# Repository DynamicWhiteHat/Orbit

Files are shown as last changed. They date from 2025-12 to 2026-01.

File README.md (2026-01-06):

# Orbit
## An ESP32-powered mini drone with autonomous following capability

## Features:
- ESP32 S3 Wroom 1u SoM
- 4x 0716 coreless motors
- MPU6050 for gyro
- QMC5883 compass
- MS5611 pressure sensor for altitude hold
- 3x SK6812 for signal LEDs
- Battery charging via USB-C
- 2x frame mounted DWM1000 for position tracking
- 1x small form factor DWM1000 board "beacon"
- Firmware based on flix by okalachev, modified to work with this project

## Why I designed this project:
I wanted to design a drone for HackClub's Blueprint program, but not just any regular drone. I wanted to add a feature that would make it stand out, something that would make it unique. So, I decided to give it the ability to autonomously follow you to an accurate degree. After doing some research, I found the DWM1000 modules and decided to design this project. I designed and redesigned the PCBs and CAD for this project many times, with each iteration improving upon the last. This project also gave me the ability to test and improve my PCB and CAD design skills. I understood a lot more about schematic connections while working on this project and learned to route much cleaner traces, even on a compact board.

## Image gallery:
<table align="center">
  <tr>
    <td align="center">
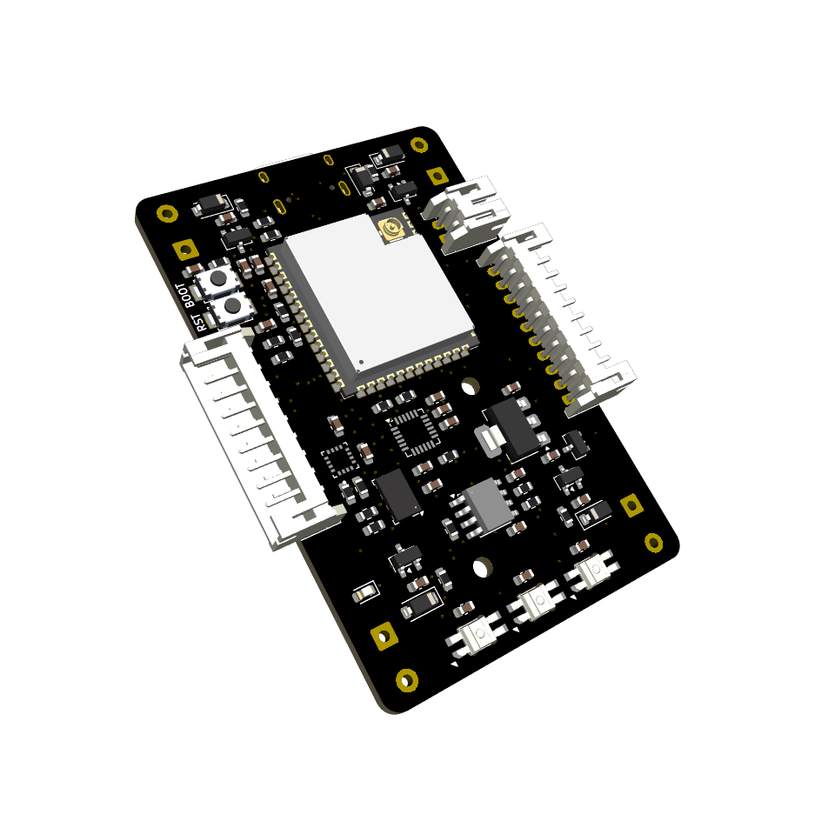
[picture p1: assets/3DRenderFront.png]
      
    </td>
    <td align="center">
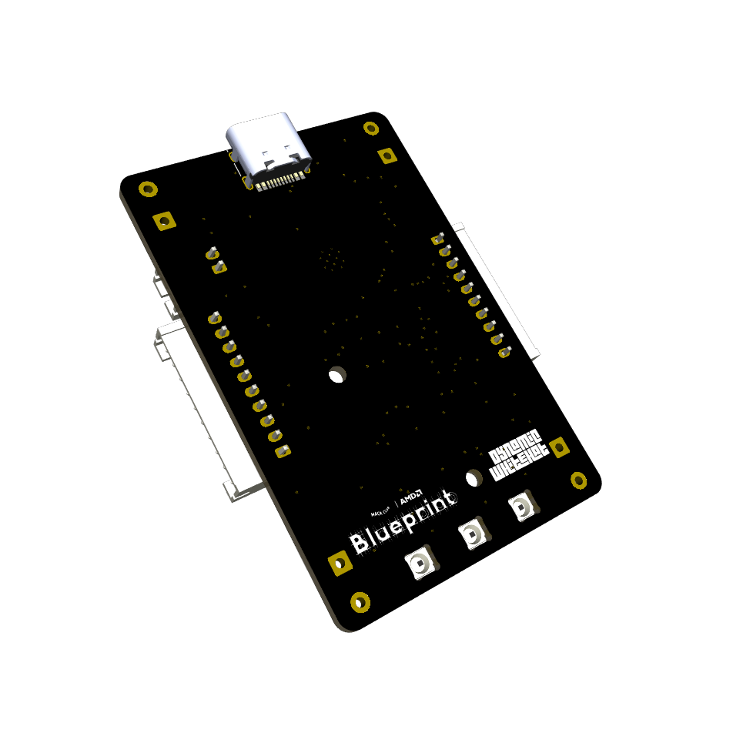
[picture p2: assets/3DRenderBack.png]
      
    </td>
  </tr>
  <tr>
    <td align="center" colspan="2">
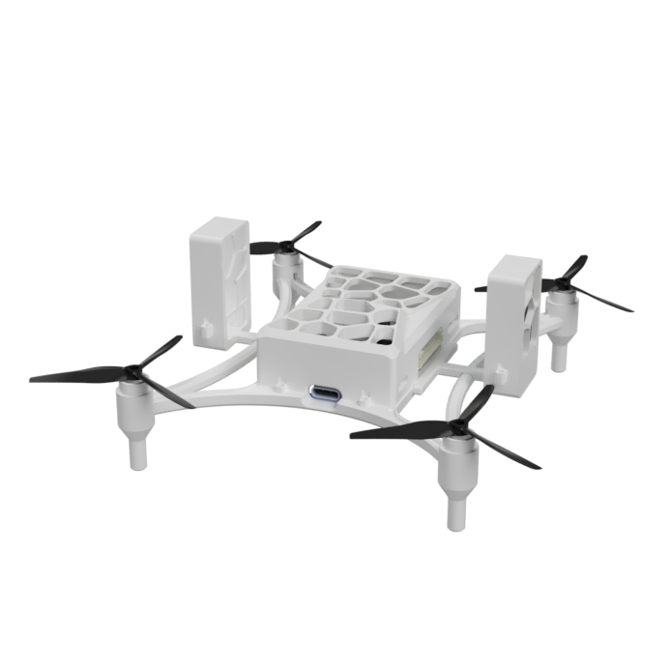
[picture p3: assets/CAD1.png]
      
    </td>
  </tr>
</table>

## Schematics And PCBS

<details>
<summary>Drone Control Board</summary>
<table align="center">
  <tr>
    <td align="center" colspan="2">
      
    </td>
  </tr>
  <tr>
     <td align="center">
      
    </td>
    <td align="center">
      
    </td>
  </tr>
</table>
</details>

<details>
<summary>Beacon Board</summary>
<table align="center">
  <tr>
    <td align="center" colspan="2">
      
    </td>
  </tr>
  <tr>
     <td align="center">
      
    </td>
    <td align="center">
     
    </td>
  </tr>
</table>
</details>

<details>
<summary>UWB Module Board</summary>
<table align="center">
  <tr>
    <td align="center" colspan="2">
      
  </tr>
  <tr>
     <td align="center">
      
    </td>
    <td align="center">
      
    </td>
  </tr>
</table>
</details>

## How It Works

The drone is powered by a custom designed PCB based on the ESP-32 S3 Wroom 1u SoM. It includes three SK6812 mini-e LEDs to serve as a status signal, located at the rear of the drone. There are three sensors located on board to help with flight. The MPU-6050 is a triple-axis accelerometer and gyroscope that is essential to help the drone fly. The MS5611 is a pressure sensor that is used to record and maintain height during flight. The final sensor, an HMC5883, is a triple-axis magnetometer that is used to report the drone's heading. The latter two sensors are reported in QGroundControl or any other flight operating station to provide information to the controller. The 0716 coreless motors are powered by a simple MOSFET circuit, designed by MaxImagination. This circuit has a small footprint and fits great for small projects, such as this drone. Autonomous flight is achieved using two DWM1000 modules mounted on the sides of the drone. These were implemented on the main PCB using 10-pin JSTs to allow modular connectivity, allowing the controller to select whether to fly with or without the ranging sensors. The DWM1000s mounted on the drone communicate with an external DWM1000 "beacon" that is with the controller or person of interest. This beacon is encased in a watch case to make it easy to wear. By sending messages between the modules, the distance between them can be calculated, allowing the beacon's location to be triangulated. This location is then set in the PID controllers, allowing the drone to autonomously navigate.

## Bill Of Materials

| Item | Description | Quantity | URL | Unit Price ($) | Total Price ($) |
|---|---|---|---|---|---|
| DWM1000 | Ranging Modules | 3 | https://www.aliexpress.us/item/3256808347510093.html | $15.13 | $50.90 |
| XIAO ESP-32 | For Beacon | 1 | Already Have | | |
| LCSC | PCB Components | 1 Order of All Parts | See LCSC BOM | | $36.92 |
| JST Connector | For DWM Connection | 1 Pack of 10 | https://www.aliexpress.us/item/3256805775471278.html | $3.09 | $3.09 |
| Battery | For Beacon | 1 | https://www.amazon.com/AKZYTUE-Battery-Rechargeable-Lithium-Connector/dp/B07TXJ4C46 | $7.79 | $7.79 |
| Battery | For Drone | 1 | https://www.amazon.com/EEMB-Battery-Rechargeable-Lithium-Connector/dp/B0B7R8CS2C | $6.99 | $7.99 |
| Motors | For Drone | 1 Pack of 4 | https://www.amazon.com/Coliao-Coreless-19000KV-Propeller-Quadcopter/dp/B0CHYDJMF2/  | $10 | $11 |
| Antenna | For Drone | 1 | https://www.aliexpress.us/item/3256806233080373.html | $1.64 | $1.64 |
| Screws | To Hold Case | 1 Pack | https://www.aliexpress.us/item/3256806233080373.html | $5.90 | $5.90 |
| JLCPCB Order  | PCBs | 1 | JLCPCB Quote | $17.16 | $17.16 |
| | | | | | $139.08 |

### LCSC Bill Of Materials
| Description | Quantity Needed | Mrf# | Minimum Order Qty. | Unit Price(USD) | Ext.Price(USD) | LCSC# | Product Link |
|---|---|---|---|---|---|---|---|
| N-Channel 20V 4A 1.2W Surface Mount SOT-23 | 4 | SI2300 | 20 | 0.0164 | 0.33 | C5224175  | https://www.lcsc.com/product-detail/C5224175.html  |
| QFN-24-EP(4x4) Accelerometers RoHS | 1 | MPU-6050 | 1 | 6.8489 | 6.85 | C24112 | https://www.lcsc.com/product-detail/C24112.html |
| 1Kpa~1.2bar QFN-8(3x5) Pressure Sensors, Transducers RoHS | 1 | MS561101BA03-50 | 1 | 5.5485 | 5.55 | C15639 | https://www.lcsc.com/product-detail/C15639.html |
| I2C LGA-16(3x3) Linear, Compass (ICs) RoHS | 1 | QMC5883P | 1 | 1.4485 | 1.45 | C2847467  | https://www.lcsc.com/product-detail/C2847467.html  |
| Red LED Indication - Discrete 2.7V~3.2V 0602 | 5 | YLED0603R | 200 | 0.0055 | 0.55 | C19171390 | https://www.lcsc.com/product-detail/C19171390.html |
| Emerald Green LED Indication - Discrete 2.7V~3.2V 0603 | 13 | YLED0603G | 200 | 0.0054 | 1.08 | C19273151 | https://www.lcsc.com/product-detail/C19273151.html |
| 2.4GHz ESP32-S3R8 -98.2dBm SMD,19.2x18mm RF Transceiver Modules and Modems RoHS | 1 | ESP32-S3-WROOM-1U-N16R8 | 1 | 5.3260 | 5.33 | C3013946  | https://www.lcsc.com/product-detail/C3013946.html  |
| 100nF ±10% 50V Ceramic Capacitor X7R 0603 | 17 | CC0603KRX7R9BB104 | 100 | 0.0025 | 0.25 | C14663 | https://www.lcsc.com/product-detail/C14663.html |
| 220nF ±10% 50V Ceramic Capacitor X7R 0603 | 1 | CL10B224KB8NNNC | 100 | 0.0081 | 0.81 | C64705 | https://www.lcsc.com/product-detail/C64705.html |
| 4.7uF ±10% 10V Ceramic Capacitor X5R 0603 | 3 | CL10A475KP8NNNC | 50 | 0.0051 | 0.26 | C1705 | https://www.lcsc.com/product-detail/C1705.html |
| 10uF ±10% 10V Ceramic Capacitor X5R 0603 | 17 | CL10A106KP8NNNC | 50 | 0.0058 | 0.29 | C19702 | https://www.lcsc.com/product-detail/C19702.html |
| 1uF ±10% 50V Ceramic Capacitor X5R 0603 | 1 | CL10A105KB8NNNC | 50 | 0.0049 | 0.25 | C15849 | https://www.lcsc.com/product-detail/C15849.html |
| 10nF ±10% 50V Ceramic Capacitor X7R 0603 | 2 | CC0603KRX7R9BB103 | 100 | 0.0022 | 0.22 | C100042 | https://www.lcsc.com/product-detail/C100042.html |
| Diode Independent 100V 300mA Surface Mount SOD-123 | 4 | 1N4148W | 100 | 0.0056 | 0.56 | C917030 | https://www.lcsc.com/product-detail/C917030.html |
| Diode Array 1 Pair Common Cathode 30V 200mA Surface Mount SOT-23 | 1 | BAT54C | 50 | 0.0063 | 0.32 | C916424 | https://www.lcsc.com/product-detail/C916424.html |
| Diode 40V 1A Surface Mount SOD-123 | 1 | 1N5819HW | 20 | 0.0237 | 0.47 | C5439970  | https://www.lcsc.com/product-detail/C5439970.html  |
| USB-C (USB TYPE-C) Receptacle Connector 16 Position Surface Mount | 1 | TYPE-C-31-M-12 | 5 | 0.1762 | 0.88 | C165948 | https://www.lcsc.com/product-detail/C165948.html |
| 100mW 10kΩ 75V ±100ppm/℃ Thick Film Resistor ±1% 0603 Chip Resistor - Surface Mount RoHS | 14 | RC0603FR-0710KL | 100 | 0.0011 | 0.11 | C98220 | https://www.lcsc.com/product-detail/C98220.html |
| 5.1kΩ ±1% 100mW 0603 Thick Film Resistor | 2 | FRC0603F5101TS | 100 | 0.0009 | 0.09 | C2907044  | https://www.lcsc.com/product-detail/C2907044.html  |
| 400mΩ ±1% 100mW 0603 Thick Film Resistor | 1 | FRL0603FR400TS | 100 | 0.0033 | 0.33 | C5126047  | https://www.lcsc.com/product-detail/C5126047.html  |
| 1kΩ ±1% 100mW 0603 Thick Film Resistor | 10 | FRC0603F1001TS | 100 | 0.0009 | 0.09 | C2907002  | https://www.lcsc.com/product-detail/C2907002.html  |
| 5kΩ 100mW 75V ±50ppm/℃ Thin Film Resistor ±0.1% 0603 Chip Resistor - Surface Mount RoHS | 1 | RT0603BRE075KL | 50 | 0.0172 | 0.86 | C862232 | https://www.lcsc.com/product-detail/C862232.html |
| 100mW 1MΩ 75V ±100ppm/℃ Thick Film Resistor ±1% 0603 Chip Resistor - Surface Mount RoHS | 5 | RC0603FR-071ML | 100 | 0.0012 | 0.12 | C105578 | https://www.lcsc.com/product-detail/C105578.html |
| Tactile Switch SPST 160gf 2mm SMD (SMT) Tab 4mm x 3mm Surface Mount | 2 | TS-1088-AR02016 | 10 | 0.0423 | 0.42 | C720477 | https://www.lcsc.com/product-detail/C720477.html |
| Lithium Battery 1A ESOP-8 Battery Management RoHS | 1 | TP4056-42-ESOP8 | 5 | 0.1784 | 0.89 | C16581 | https://www.lcsc.com/product-detail/C16581.html |
| Positive Fixed 3.3V SOT-223 Voltage Regulators - Linear, Low Drop Out (LDO) Regulators RoHS | 5 | AP7361C-33E-13 | 5 | 0.2462 | 1.23 | C500795 | https://www.lcsc.com/product-detail/C500795.html |
| 220kΩ ±1% 100mW 0603 Thick Film Resistor | 2 | FRC0603F2203TS | 100 | 0.0010 | 0.10 | C2907013  | https://www.lcsc.com/product-detail/C2907013.html  |
| 470Ω ±1% 100mW 0603 Thick Film Resistor | 12 | 0603WAF4700T5E | 100 | 0.0012 | 0.12 | C23179 | https://www.lcsc.com/product-detail/C23179.html |
| Slide Switch SPDT 300mA @ 5V Surface Mount, Right Angle Rectangular Columnar | 1 | SSSS811101 | 5 | 0.1408 | 0.70 | C109335 | https://www.lcsc.com/product-detail/C109335.html |
| Connector Header 2 position 2mm Pitch 2A Right Angle -25℃~+85℃ | 1 | S2B-PH-K-S(LF)(SN) | 20 | 0.0351 | 0.70 | C17375 | https://lcsc.com/product-detail/C17375 |

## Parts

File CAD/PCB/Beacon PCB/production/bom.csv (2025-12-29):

Designator | Footprint | Quantity | Value | LCSC Part #
C1 | 0603 | 1 | 10uF
C2 | 0603 | 1 | 0.1uF
D1, D2, D3, D4 | 0603 | 4 | LED
DWM1 | DWM1000 | 1 | DWM1000
J1 | SolderWire-0.5sqmm_1x02_P4.8mm_D0.9mm_OD2.3mm | 1 | Conn_01x02_Socket
R1, R2, R3 | 0603 | 3 | 1k
R10, R8 | 0603 | 2 | 220k
R4, R5, R6, R7 | 0603 | 4 | 470R
S1 | SW_SSSS811101 | 1 | JS102011CQN
U2 | XIAO-ESP32S3-SMD | 1 | XIAO-ESP32-S3-SMD

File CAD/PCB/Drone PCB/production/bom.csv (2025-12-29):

Designator | Footprint | Quantity | Value | LCSC Part #
C1, C2, C3, C4, C9 | 0603 | 5 | 100nF
C10, C18, C21, C22, C23, C24, C25, C5, C7 | 0603 | 9 | 0.1uF
C12, C16, C17 | 0603 | 3 | 4.7uF
C13, C14, C15, C19 | 0603 | 4 | 10uF
C20 | 0603 | 1 | 1uF
C6, C8 | 0603 | 2 | 0.01uF
D1, D2, D3, D4 | D_SOD-123 | 4 | 1N4148
D10 | SOT-23 | 1 | BAT54C
D5 | D_SOD-123 | 1 | 1N5819HW-7-F
D9 | 0603 | 1 | LED
J1, J2, J3, J4 | SolderWire-0.5sqmm_1x02_P4.8mm_D0.9mm_OD2.3mm | 4 | Conn_01x02_Socket
J10, J6 | JST_PH_S10B-PH-K_1x10_P2.00mm_Horizontal | 2 | Conn_01x10_Socket
J7 | USB_C_Receptacle_HRO_TYPE-C-31-M-12 | 1 | USB_C_Receptacle_USB2.0_16P
J8 | JST_PH_S2B-PH-K_1x02_P2.00mm_Horizontal | 1 | Conn_01x02
LED1, LED2, LED3 | LED_6028R | 3 | SK6812MINI-E
Q1, Q2, Q3, Q4 | SOT-23 | 4 | Si2319CDS
R1, R10, R11, R12, R13, R2, R20, R21, R22, R3, R4, R7, R8, R9 | 0603 | 14 | 10k
R14, R15 | 0603 | 2 | 5.1k
R16 | 0603 | 1 | 0.4R
R17 | 0603 | 1 | 1k
R19 | 0603 | 1 | 5k
R5, R6 | 0603 | 2 | 1M
SW1, SW2 | SW_TS-1088-AR02016 | 2 | SW_Push
U2 | InvenSense_QFN-24_4x4mm_P0.5mm | 1 | MPU-6050
U3 | LGA-8_3x5mm_P1.25mm | 1 | MS5611-01BA
U4 | XDCR_HMC5883L-TR | 1 | HMC5883L-TR
U5 | XCVR_ESP32-S3-WROOM-1U | 1 | ESP32-S3-WROOM-1U
U6 | SOIC-8-1EP_3.9x4.9mm_P1.27mm_EP2.41x3.3mm_ThermalVias | 1 | TP4056-42-ESOP8
U7 | SOT-223-3_TabPin2 | 1 | AP7361C-33E

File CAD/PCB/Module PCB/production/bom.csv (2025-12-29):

Designator | Footprint | Quantity | Value | LCSC Part #
C1 | 0603 | 1 | 10uF
C2 | 0603 | 1 | 0.1uF
D1, D2, D3, D4 | 0603 | 4 | LED
DWM1 | DWM1000 | 1 | DWM1000
J1, J2 | SolderWire-0.5sqmm_1x04_P4.8mm_D0.9mm_OD2.3mm | 2 | Conn_01x04_Socket
J3 | SolderWire-0.5sqmm_1x02_P4.8mm_D0.9mm_OD2.3mm | 1 | Conn_01x02_Socket
R1, R2, R3 | 0603 | 3 | 1k
R4, R5, R6, R7 | 0603 | 4 | 470R

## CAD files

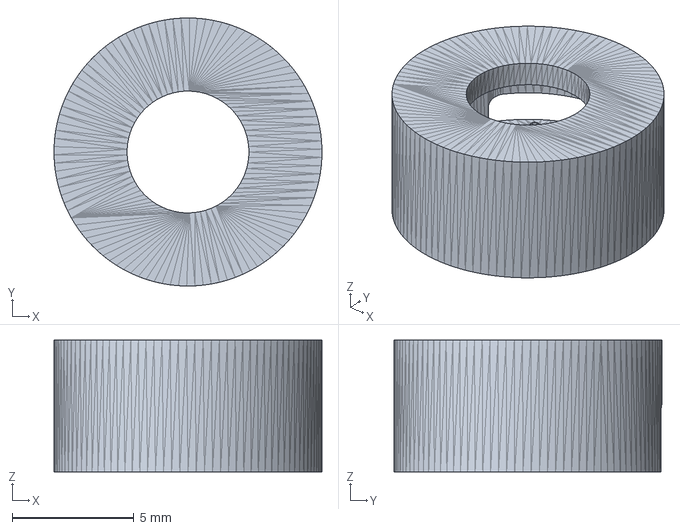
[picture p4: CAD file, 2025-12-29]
CAD/Frame/STEP/Cap.step
11.0 x 11.0 x 5.40 mm

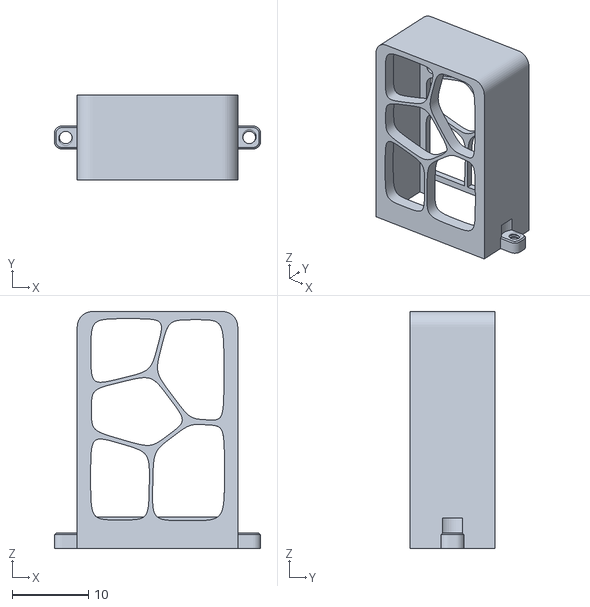
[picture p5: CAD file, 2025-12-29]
CAD/Frame/STL/UWBHolderTop.stl
27.0 x 11.1 x 31.0

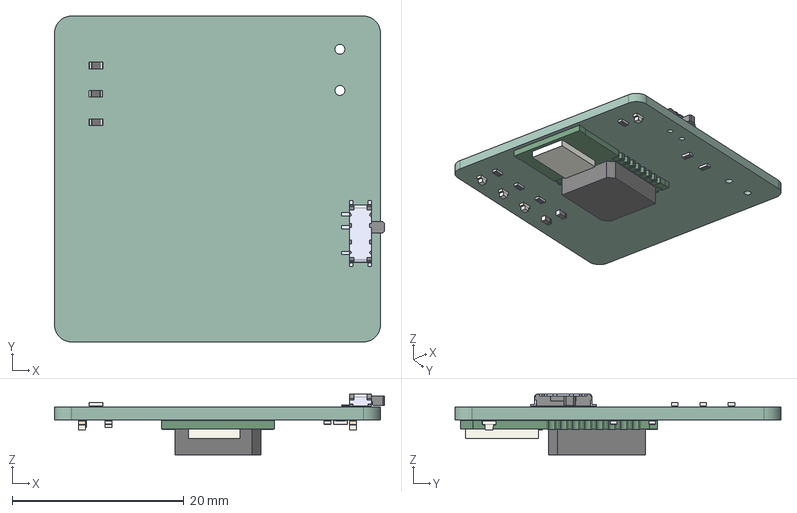
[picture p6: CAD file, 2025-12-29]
CAD/PCB/Beacon PCB/UWB Fly.step
38.5 x 38.0 x 7.08 mm
R_0603_1608Metric x 9
SSSS811101
LED_0603_1608Metric x 4
C_0603_1608Metric x 2
DWM1000
UWB Fly_PCB

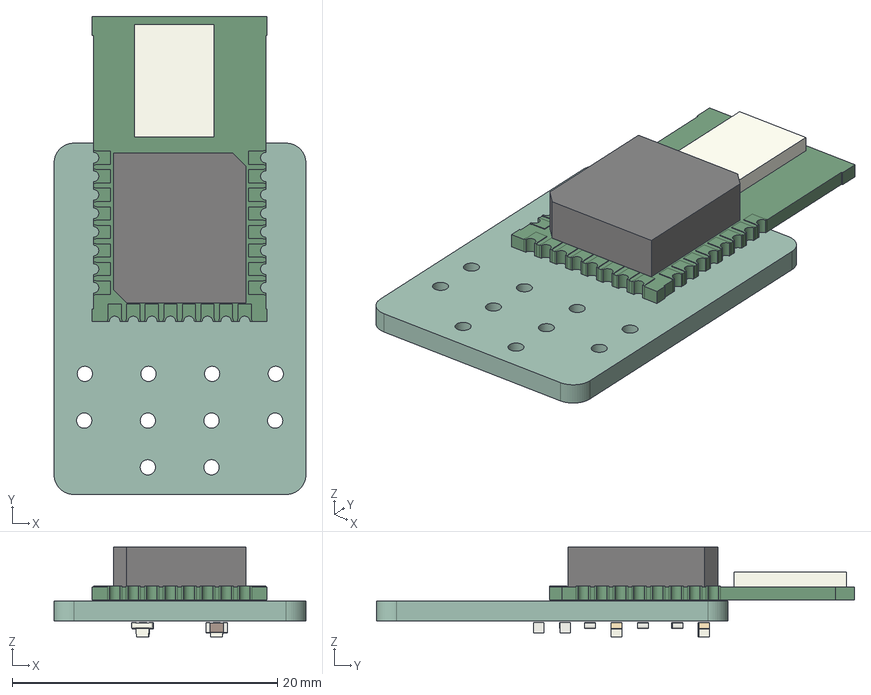
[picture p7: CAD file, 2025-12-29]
CAD/PCB/Module PCB/UWB Fly Module.step
19.0 x 36.1 x 6.78 mm
DWM1000
R_0603_1608Metric x 7
LED_0603_1608Metric x 4
C_0603_1608Metric x 2
UWB Fly Module_PCB

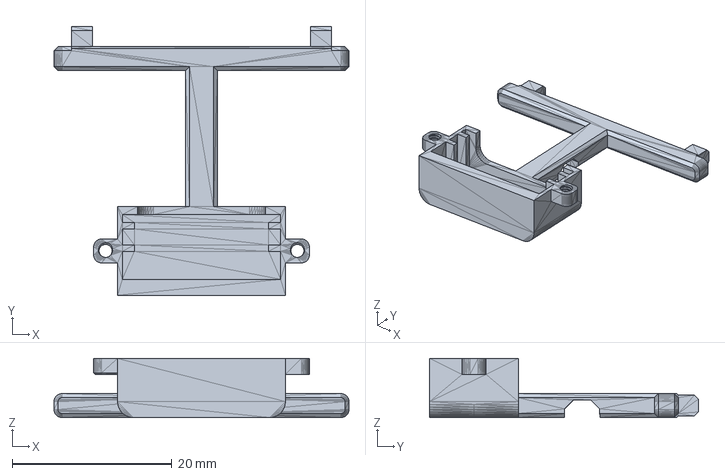
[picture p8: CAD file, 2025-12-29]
CAD/Frame/STEP/UWBHolderBottom.step
36.9 x 33.6 x 7.40 mm

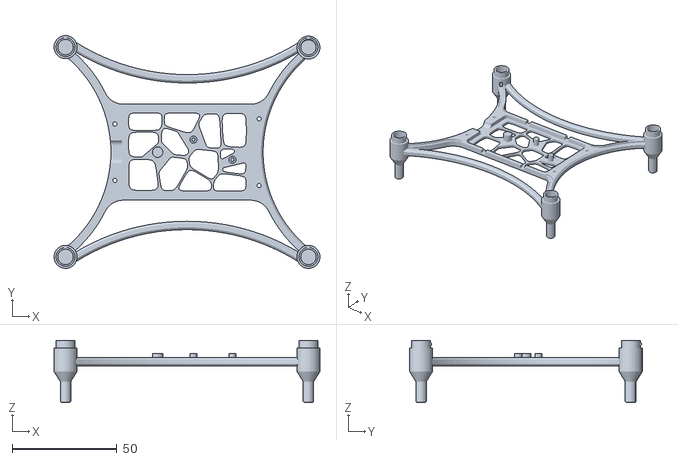
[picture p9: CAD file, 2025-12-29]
CAD/Frame/STL/Bottom.stl
126.8 x 111.0 x 29.6

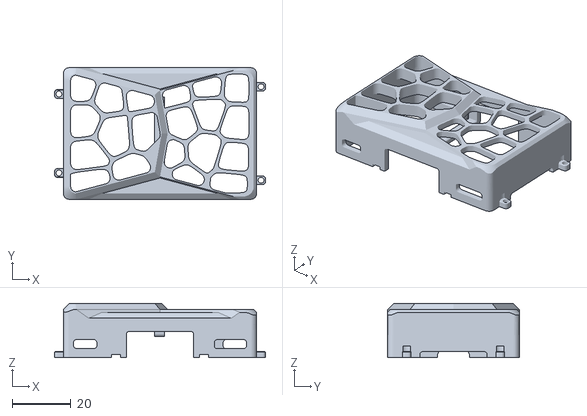
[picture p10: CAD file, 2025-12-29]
CAD/Frame/STL/Top.stl
71.8 x 44.8 x 18.4

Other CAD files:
CAD/Frame/STL/Cap.stl
CAD/Frame/STL/UWBHolderBottom.stl

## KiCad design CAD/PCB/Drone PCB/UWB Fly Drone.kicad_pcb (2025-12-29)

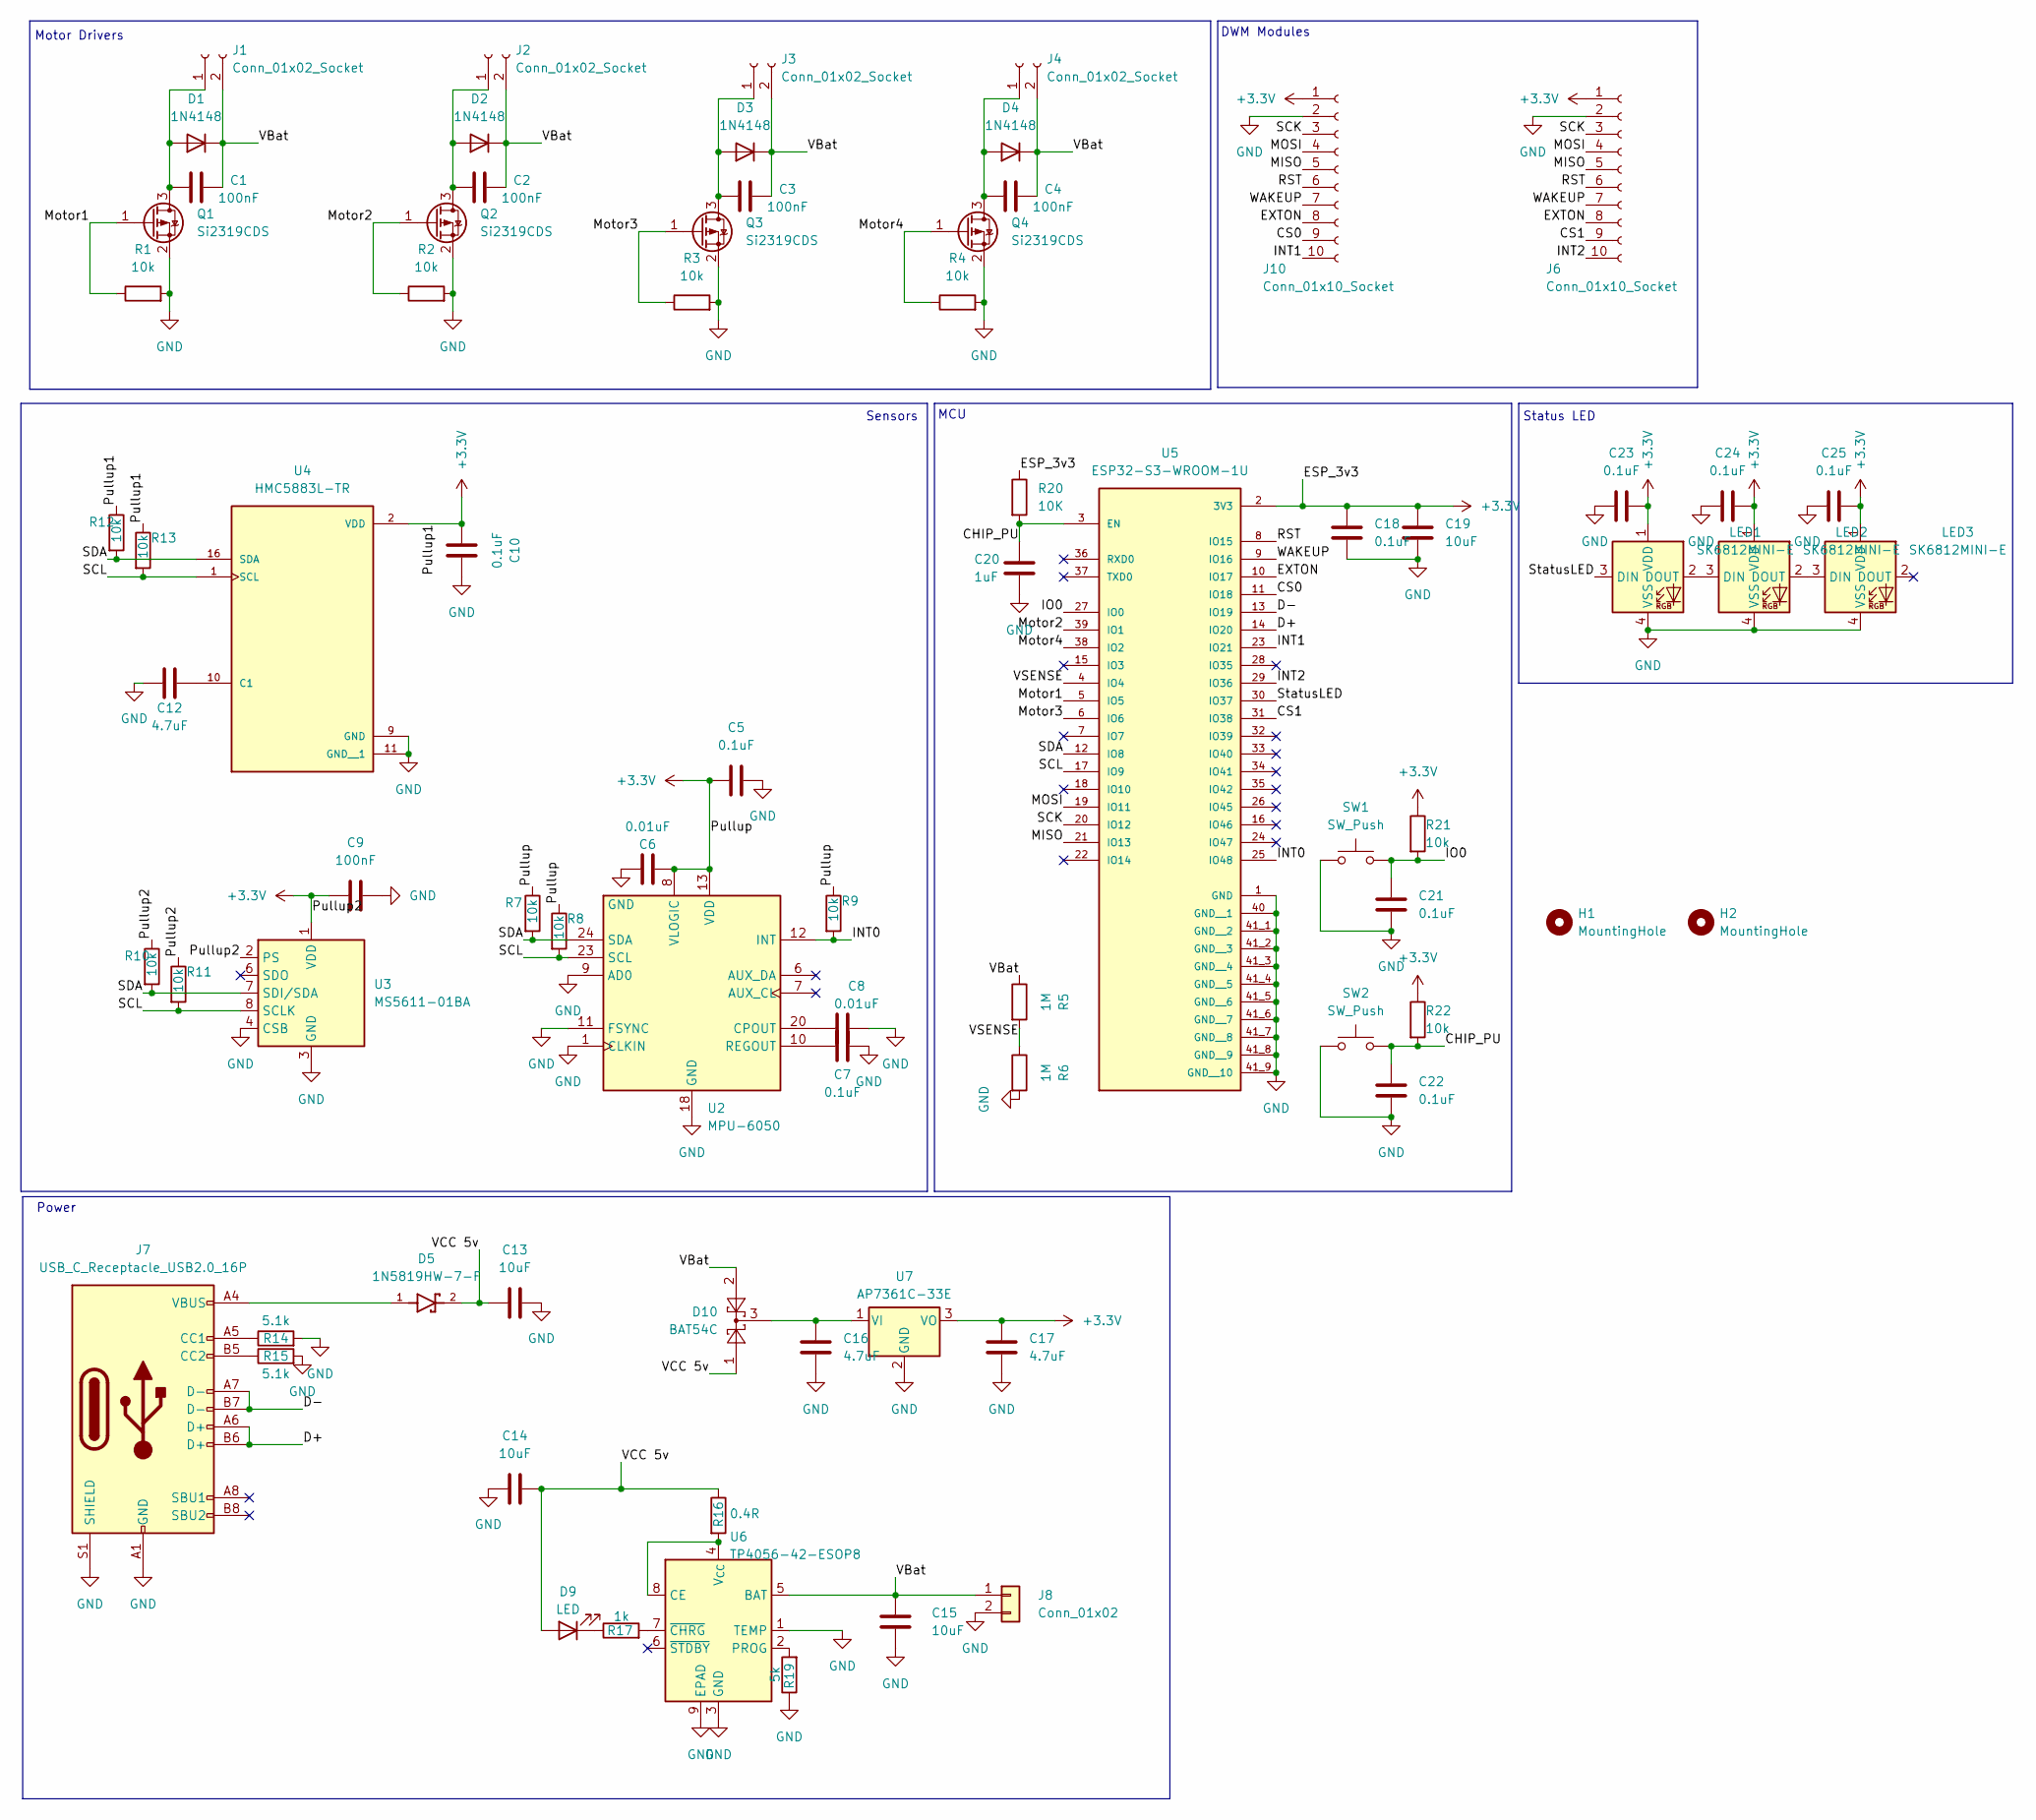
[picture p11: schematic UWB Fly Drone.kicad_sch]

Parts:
C1, C2, C3, C4, C9: 100nF; C_0603_1608Metric
C5, C7, C10, C18, C21, C22, C23, C24, C25: 0.1uF; C_0603_1608Metric
C6, C8: 0.01uF; C_0603_1608Metric
C12, C16, C17: 4.7uF; C_0603_1608Metric
C13, C14, C15, C19: 10uF; C_0603_1608Metric
C20: 1uF; C_0603_1608Metric
D1, D2, D3, D4: 1N4148; D_SOD-123
D5: 1N5819HW-7-F; D_SOD-123; PARTREV 18-2
D9: LED; LED_0603_1608Metric
D10: BAT54C; SOT-23
H1, H2: MountingHole; MountingHole_2.2mm_M2
J1, J2, J3, J4: Conn_01x02_Socket; SolderWire-0.5sqmm_1x02_P4.8mm_D0.9mm_OD2.3mm
J6, J10: Conn_01x10_Socket; JST_PH_S10B-PH-K_1x10_P2.00mm_Horizontal
J7: USB_C_Receptacle_USB2.0_16P; USB_C_Receptacle_HRO_TYPE-C-31-M-12
J8: Conn_01x02; JST_PH_S2B-PH-K_1x02_P2.00mm_Horizontal
LED1, LED2, LED3: SK6812MINI-E; LED_6028R
Q1, Q2, Q3, Q4: Si2319CDS; SOT-23
R1, R2, R3, R4, R7, R8, R9, R10, R11, R12, R13, R21, R22: 10k; R_0603_1608Metric
R5, R6: 1M; R_0603_1608Metric
R14, R15: 5.1k; R_0603_1608Metric
R16: 0.4R; R_0603_1608Metric
R17: 1k; R_0603_1608Metric
R19: 5k; R_0603_1608Metric
R20: 10K; R_0603_1608Metric
SW1, SW2: SW_Push; SW_TS-1088-AR02016
U2: MPU-6050; InvenSense_QFN-24_4x4mm_P0.5mm
U3: MS5611-01BA; LGA-8_3x5mm_P1.25mm
U4: HMC5883L-TR; XDCR_HMC5883L-TR; PARTREV E
U5: ESP32-S3-WROOM-1U; XCVR_ESP32-S3-WROOM-1U; PARTREV v0.6
U6: TP4056-42-ESOP8; SOIC-8-1EP_3.9x4.9mm_P1.27mm_EP2.41x3.3mm_ThermalVias
U7: AP7361C-33E; SOT-223-3_TabPin2

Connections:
+3.3V: C5.1, C6.1, C9.1, C10.1, C17.1, C18.1, C19.1, C23.2, C24.2, C25.2, J6.1, J10.1, LED1.1 (VDD), LED2.1 (VDD), LED3.1 (VDD), R7.1, R8.1, R9.1, R10.1, R11.1, R12.1, R13.1, R20.1, R21.1, R22.1, U2.8 (VLOGIC), U2.13 (VDD), U3.1 (VDD), U3.2 (PS), U4.2 (VDD), U5.2 (3V3), U7.3 (VO)
/CHIP_PU: C20.1, C22.1, R20.2, R22.2, SW2.2, U5.3 (EN)
/CS0: J10.9, U5.11 (IO18)
/CS1: J6.9, U5.31 (IO38)
/D+: J7.A6 (D+), J7.B6 (D+), U5.14 (IO20)
/D-: J7.A7 (D-), J7.B7 (D-), U5.13 (IO19)
/EXTON: J6.8, J10.8, U5.10 (IO17)
/INT0: R9.2, U2.12 (INT), U5.25 (IO48)
/INT1: J10.10, U5.23 (IO21)
/INT2: J6.10, U5.29 (IO36)
/IO0: C21.1, R21.2, SW1.2, U5.27 (IO0)
/MISO: J6.5, J10.5, U5.21 (IO13)
/MOSI: J6.4, J10.4, U5.19 (IO11)
/Motor1: Q1.1 (G), R1.1, U5.5 (IO5)
/Motor2: Q2.1 (G), R2.1, U5.39 (IO1)
/Motor3: Q3.1 (G), R3.1, U5.6 (IO6)
/Motor4: Q4.1 (G), R4.1, U5.38 (IO2)
/RST: J6.6, J10.6, U5.8 (IO15)
/SCK: J6.3, J10.3, U5.20 (IO12)
/SCL: R8.2, R11.2, R13.2, U2.23 (SCL), U3.8 (SCLK), U4.1 (SCL), U5.17 (IO9)
/SDA: R7.2, R10.2, R12.2, U2.24 (SDA), U3.7 (SDI/SDA), U4.16 (SDA), U5.12 (IO8)
/StatusLED: LED1.3 (DIN), U5.30 (IO37)
/VBat: C1.2, C2.2, C3.2, C4.2, C15.1, D1.1 (K), D2.1 (K), D3.1 (K), D4.1 (K), D10.2, J1.2, J2.2, J3.2, J4.2, J8.1, R5.1, U6.5 (BAT)
/VCC 5v: C13.1, C14.2, D5.2, D9.2 (A), D10.1, R16.1
/VSENSE: R5.2, R6.1, U5.4 (IO4)
/WAKEUP: J6.7, J10.7, U5.9 (IO16)
GND: C5.2, C6.2, C7.2, C8.2, C9.2, C10.2, C12.1, C13.2, C14.1, C15.2, C16.2, C17.2, C18.2, C19.2, C20.2, C21.2, C22.2, C23.1, C24.1, C25.1, J6.2, J7.A1 (GND), J7.A12 (GND), J7.B1 (GND), J7.B12 (GND), J7.S1 (SHIELD), J8.2, J10.2, LED1.4 (VSS), LED2.4 (VSS), LED3.4 (VSS), Q1.2 (S), Q2.2 (S), Q3.2 (S), Q4.2 (S), R1.2, R2.2, R3.2, R4.2, R6.2, R14.2, R15.2, R19.1, SW1.1, SW2.1, U2.1 (CLKIN), U2.9 (AD0), U2.11 (FSYNC), U2.18 (GND), U3.3 (GND), U3.4 (CSB), U3.5 (CSB), U4.9 (GND), U4.11 (GND__1), U5.1 (GND), U5.40 (GND__1), U5.41_1 (GND__2), U5.41_2 (GND__3), U5.41_3 (GND__4), U5.41_4 (GND__5), U5.41_5 (GND__6), U5.41_6 (GND__7), U5.41_7 (GND__8), U5.41_8 (GND__9), U5.41_9 (GND__10), U6.1 (TEMP), U6.3 (GND), U6.9 (EPAD), U7.2 (GND)
unnamed: C1.1, D1.2 (A), J1.1, Q1.3 (D)
unnamed: C2.1, D2.2 (A), J2.1, Q2.3 (D)
unnamed: C3.1, D3.2 (A), J3.1, Q3.3 (D)
unnamed: C4.1, D4.2 (A), J4.1, Q4.3 (D)
unnamed: D5.1, J7.A4 (VBUS), J7.A9 (VBUS), J7.B4 (VBUS), J7.B9 (VBUS)
unnamed: D9.1 (K), R17.1
unnamed: J7.A5 (CC1), R14.1
unnamed: J7.B5 (CC2), R15.1
unnamed: LED1.2 (DOUT), LED2.3 (DIN)
unnamed: LED2.2 (DOUT), LED3.3 (DIN)
unnamed: C8.1, U2.20 (CPOUT)
unnamed: C7.1, U2.10 (REGOUT)
unnamed: C12.2, U4.10 (C1)
unnamed: R16.2, U6.4 (V_{CC}), U6.8 (CE)
unnamed: R19.2, U6.2 (PROG)
unnamed: R17.2, U6.7 (~CHRG)
unnamed: C16.1, D10.3, U7.1 (VI)

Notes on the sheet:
Status LED
MCU
Motor Drivers
DWM Modules
Power
Sensors

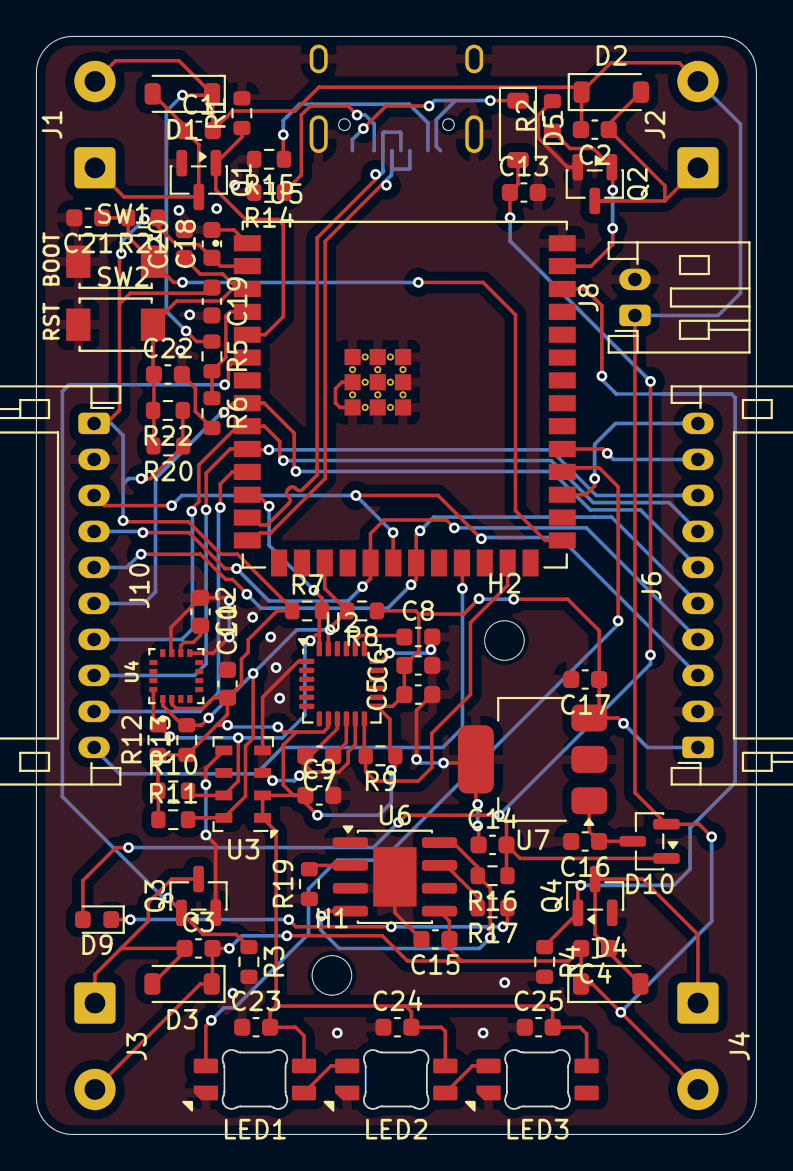
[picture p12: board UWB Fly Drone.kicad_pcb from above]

Board: 2 copper layers, 40.0 x 61.0 mm, 77 parts (1 on the bottom side), 44 nets.

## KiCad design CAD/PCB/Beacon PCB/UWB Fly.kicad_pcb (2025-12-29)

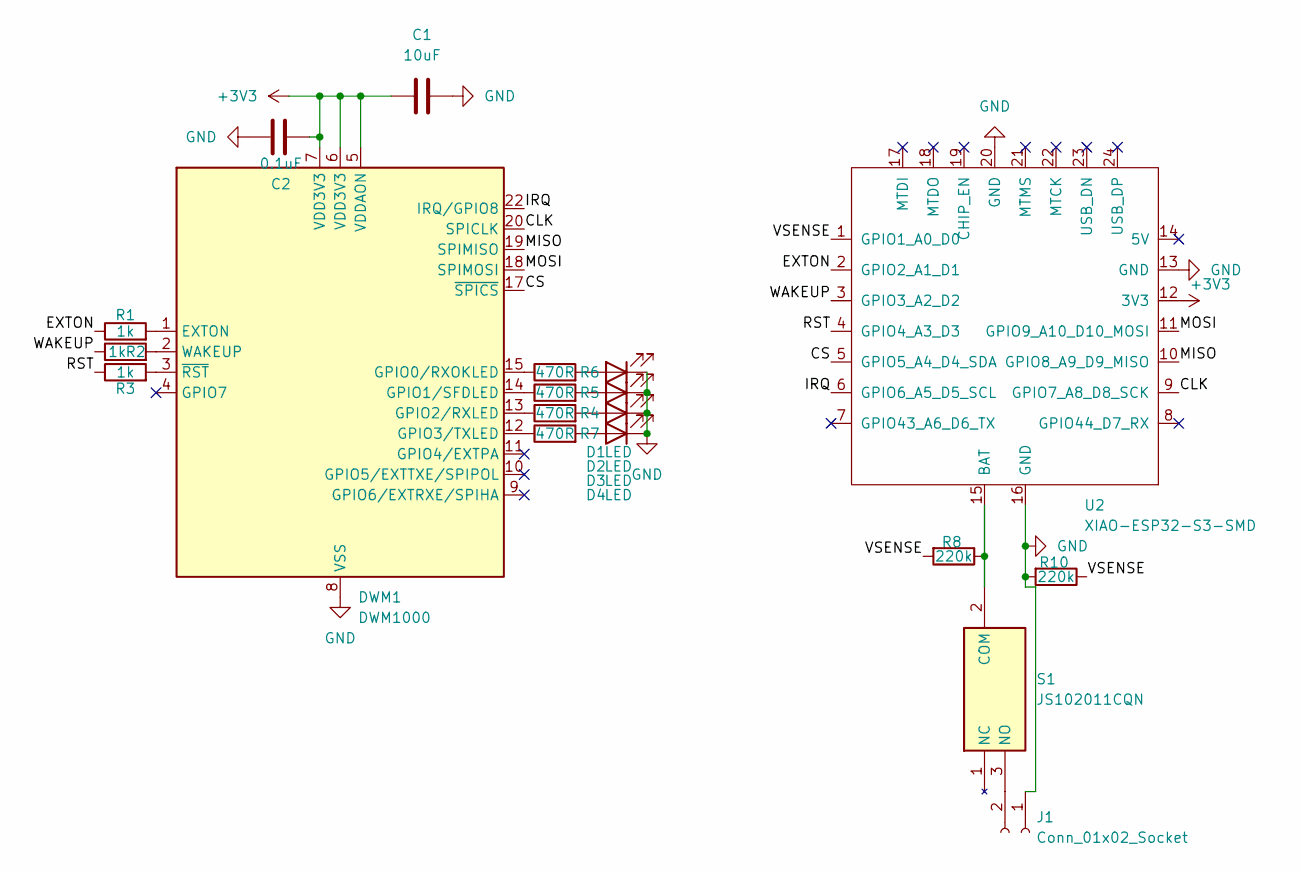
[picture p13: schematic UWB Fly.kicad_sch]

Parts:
C1: 10uF; C_0603_1608Metric
C2: 0.1uF; C_0603_1608Metric
D1, D2, D3, D4: LED; LED_0603_1608Metric
DWM1: DWM1000
J1: Conn_01x02_Socket; SolderWire-0.5sqmm_1x02_P4.8mm_D0.9mm_OD2.3mm
R1, R2, R3: 1k; R_0603_1608Metric
R4, R5, R6, R7: 470R; R_0603_1608Metric
R8, R10: 220k; R_0603_1608Metric
S1: JS102011CQN; SW_SSSS811101; Mouser Part Number 611-JS102011CQN
U2: XIAO-ESP32-S3-SMD; XIAO-ESP32S3-SMD

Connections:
+3V3: C1.1, C2.1, DWM1.5 (VDDAON), DWM1.6 (VDD3V3), DWM1.7 (VDD3V3), U2.12 (3V3)
/CLK: DWM1.20 (SPICLK), U2.9 (GPIO7_A8_D8_SCK)
/CS: DWM1.17 (~SPICS), U2.5 (GPIO5_A4_D4_SDA)
/EXTON: R1.1, U2.2 (GPIO2_A1_D1)
/IRQ: DWM1.22 (IRQ/GPIO8), U2.6 (GPIO6_A5_D5_SCL)
/MISO: DWM1.19 (SPIMISO), U2.10 (GPIO8_A9_D9_MISO)
/MOSI: DWM1.18 (SPIMOSI), U2.11 (GPIO9_A10_D10_MOSI)
/RST: R3.1, U2.4 (GPIO4_A3_D3)
/VSENSE: R8.2, R10.1, U2.1 (GPIO1_A0_D0)
/WAKEUP: R2.1, U2.3 (GPIO3_A2_D2)
GND: C1.2, C2.2, D1.1 (K), D2.1 (K), D3.1 (K), D4.1 (K), DWM1.8 (VSS), DWM1.16 (VSS), DWM1.21 (VSS), DWM1.23 (VSS), DWM1.24 (VSS), J1.1, R10.2, U2.13 (GND), U2.16 (GND), U2.20 (GND)
unnamed: D1.2 (A), R6.2
unnamed: D2.2 (A), R5.2
unnamed: D3.2 (A), R4.2
unnamed: D4.2 (A), R7.2
unnamed: DWM1.1 (EXTON), R1.2
unnamed: DWM1.15 (GPIO0/RXOKLED), R6.1
unnamed: DWM1.14 (GPIO1/SFDLED), R5.1
unnamed: DWM1.13 (GPIO2/RXLED), R4.1
unnamed: DWM1.12 (GPIO3/TXLED), R7.1
unnamed: DWM1.2 (WAKEUP), R2.2
unnamed: DWM1.3 (~RST), R3.2
unnamed: J1.2, S1.3 (NO)
unnamed: R8.1, S1.2 (COM), U2.15 (BAT)

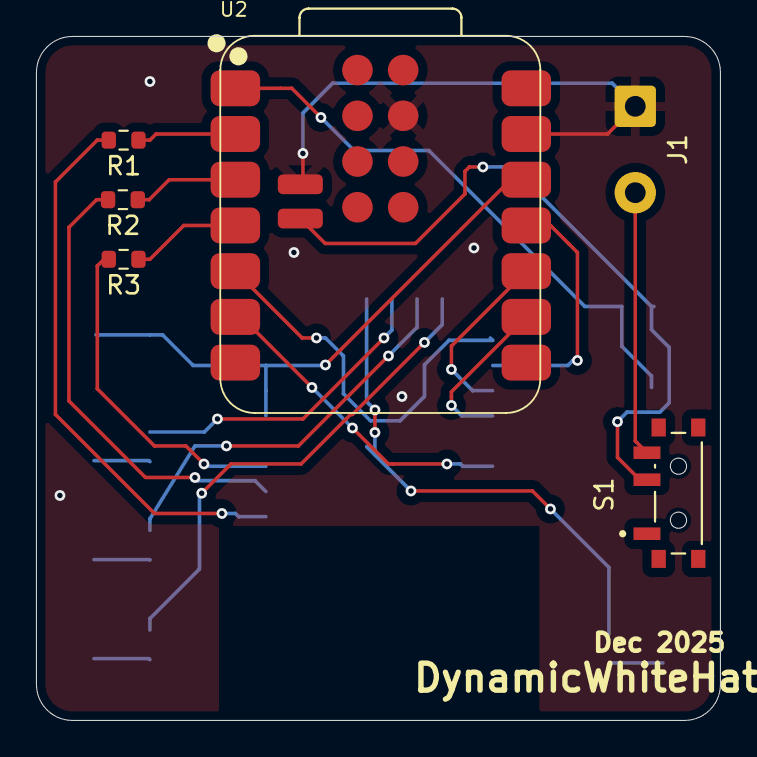
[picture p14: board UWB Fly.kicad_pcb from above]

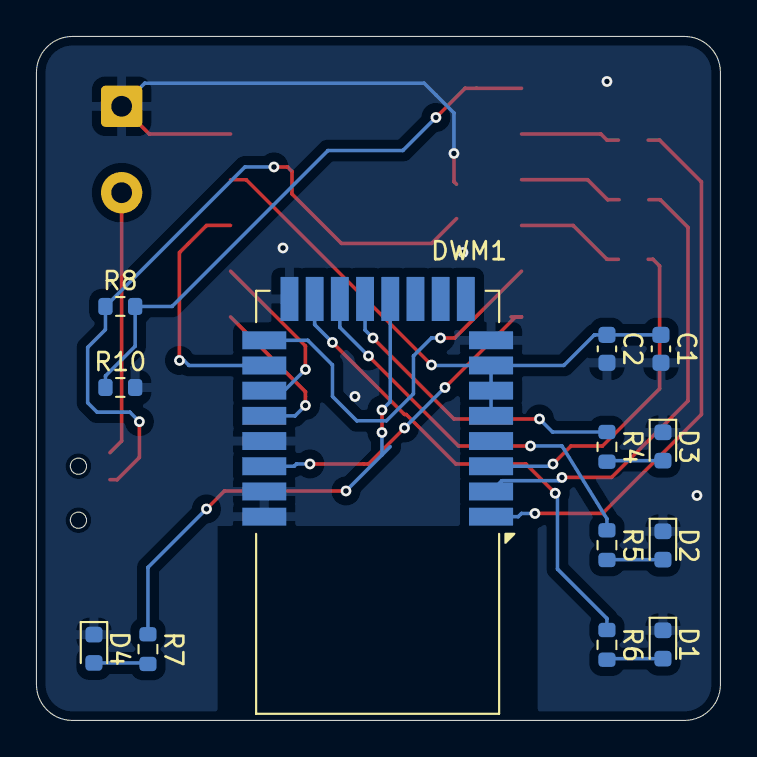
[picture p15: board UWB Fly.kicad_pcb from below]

Board: 2 copper layers, 38.0 x 38.0 mm, 19 parts (13 on the bottom side), 24 nets.

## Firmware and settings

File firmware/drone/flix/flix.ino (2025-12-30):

// Copyright (c) 2023 Oleg Kalachev <okalachev@gmail.com>
// Repository: https://github.com/okalachev/flix

// Main firmware file

#include "vector.h"
#include "quaternion.h"
#include "util.h"
#include "config.h"

#define WIFI_ENABLED 1

float t = NAN; // current step time, s
float dt; // time delta from previous step, s
float controlRoll, controlPitch, controlYaw, controlThrottle; // pilot's inputs, range [-1, 1]
float controlMode = NAN;
Vector gyro; // gyroscope data
Vector acc; // accelerometer data, m/s/s
Vector rates; // filtered angular rates, rad/s
Quaternion attitude; // estimated attitude
bool landed; // are we landed and stationary
float motors[4]; // normalized motors thrust in range [0..1]

void setup() {
	setupLED();
	setLED(2);
	Serial.begin(115200);
	print("Initializing flix\n");
	disableBrownOut();
	setupParameters();
	#if BATTERY_ENABLED
		setupBattery();
	#endif
	#if BAROMETER_ENABLED
		setupBarometer();
	#endif
	setupMotors();
	#if WIFI_ENABLED
		setupWiFi();
	#endif
	setupCompass();
	setupLocator();
	setupIMU();
	setupRC();
	setLED(4);
	print("Initializing complete\n");
}

void loop() {
	readIMU();
	loopCompass();
	step();
	readRC();
	estimate();
	control();
	#if BATTERY_ENABLED
		loopBattery();
	#endif
	#if BAROMETER_ENABLED
		loopBarometer();
	#endif
		sendMotors();
		handleInput();
	#if WIFI_ENABLED
		processMavlink();
	#endif
	logData();
	syncParameters();
}

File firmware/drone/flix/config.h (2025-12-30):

#define BAROMETER_UPDATE_INTERVAL 1.0
#define BAROMETER_ENABLED 1
#define BATTERY_ENABLED 1
#define BATTERY_UPDATE_INTERVAL 0.1                          
#define BATTERY_CELLS 1                                      
#define BATTERY_MIN_LEVEL 3400 * BATTERY_CELLS               
#define BATTERY_MAX_LEVEL 4200 * BATTERY_CELLS               
#define BATTERY_DISARMED_VOLTAGE_THRESHOLD BATTERY_MIN_LEVEL 
#define BATTERY_DISARMED_CURRENT_THRESHOLD_MIN 10            
#define BATTERY_DISARMED_CURRENT_THRESHOLD_MAX 15000         
#define BATTERY_MAVLINK_STATUS_LOW 3500 * BATTERY_CELLS
#define BATTERY_MAVLINK_STATUS_CRITICAL 3300 * BATTERY_CELLS
#define BATTERY_MAVLINK_STATUS_EMERGENCY BATTERY_MIN_LEVEL
#define UWB_SPACING 0.099394;

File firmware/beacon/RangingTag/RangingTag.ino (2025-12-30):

#include <SPI.h>
#include <DW1000.h>

#define PIN_RST 4
#define PIN_IRQ 6
#define PIN_SS  5

#define POLL 0
#define LEN_DATA 16

byte data[LEN_DATA];

void setup() {
    Serial.begin(115200);
    DW1000.begin(PIN_IRQ, PIN_RST);
    DW1000.select(PIN_SS);

    DW1000.newConfiguration();
    DW1000.setDefaults();
    DW1000.setDeviceAddress(10);  // arbitrary address for the beacon
    DW1000.setNetworkId(10);
    DW1000.enableMode(DW1000.MODE_LONGDATA_RANGE_LOWPOWER);
    DW1000.commitConfiguration();

    Serial.println("Beacon initialized...");
}

void loop() {
    // transmit a simple POLL packet
    DW1000.newTransmit();
    DW1000.setDefaults();
    data[0] = POLL;
    DW1000.setData(data, LEN_DATA);
    DW1000.startTransmit();
    Serial.println("Beacon transmitted POLL");

    delay(100); // transmit every 100ms
}

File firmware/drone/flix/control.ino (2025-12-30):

// Copyright (c) 2023 Oleg Kalachev <okalachev@gmail.com>
// Repository: https://github.com/okalachev/flix

// Flight control

#include "vector.h"
#include "quaternion.h"
#include "pid.h"
#include "lpf.h"
#include "util.h"

#define PITCHRATE_P 0.05
#define PITCHRATE_I 0.2
#define PITCHRATE_D 0.001
#define PITCHRATE_I_LIM 0.3
#define ROLLRATE_P PITCHRATE_P
#define ROLLRATE_I PITCHRATE_I
#define ROLLRATE_D PITCHRATE_D
#define ROLLRATE_I_LIM PITCHRATE_I_LIM
#define YAWRATE_P 0.3
#define YAWRATE_I 0.0
#define YAWRATE_D 0.0
#define YAWRATE_I_LIM 0.3
#define ROLL_P 6
#define ROLL_I 0
#define ROLL_D 0
#define PITCH_P ROLL_P
#define PITCH_I ROLL_I
#define PITCH_D ROLL_D
#define YAW_P 3
#define YAW_BEACON_P 1.0;
#define YAW_BEACON_I 0.0;
#define YAW_BEACON_D 0.0;
#define PITCHRATE_MAX radians(360)
#define ROLLRATE_MAX radians(360)
#define YAWRATE_MAX radians(300)
#define TILT_MAX radians(30)
#define RATES_D_LPF_ALPHA 0.2 // cutoff frequency ~ 40 Hz

const int RAW = 0, ACRO = 1, STAB = 2, AUTO = 3, BEACON = 4; // flight modes
int mode = STAB;
bool armed = false;

PID rollRatePID(ROLLRATE_P, ROLLRATE_I, ROLLRATE_D, ROLLRATE_I_LIM, RATES_D_LPF_ALPHA);
PID pitchRatePID(PITCHRATE_P, PITCHRATE_I, PITCHRATE_D, PITCHRATE_I_LIM, RATES_D_LPF_ALPHA);
PID yawRatePID(YAWRATE_P, YAWRATE_I, YAWRATE_D);
PID rollPID(ROLL_P, ROLL_I, ROLL_D);
PID pitchPID(PITCH_P, PITCH_I, PITCH_D);
PID yawPID(YAW_P, 0, 0);
PID yawBeaconPID(1.0, 0, 0);
Vector maxRate(ROLLRATE_MAX, PITCHRATE_MAX, YAWRATE_MAX);
float tiltMax = TILT_MAX;

Quaternion attitudeTarget;
Vector ratesTarget;
Vector ratesExtra; // feedforward rates
Vector torqueTarget;
float thrustTarget;

extern const int MOTOR_REAR_LEFT, MOTOR_REAR_RIGHT, MOTOR_FRONT_RIGHT, MOTOR_FRONT_LEFT;
extern float controlRoll, controlPitch, controlThrottle, controlYaw, controlMode;

const float TARGET_HEIGHT_FT = 5.0f; 
const float ALT_HOVER_THRUST = 0.5f; 
const float ALT_KP = 0.12f;          

const float ALT_MIN_THRUST = 0.25f;
const float ALT_MAX_THRUST = 0.7f;

void control() {
	interpretControls();
	failsafe();
	controlAttitude();
	controlRates();
	controlTorque();
}

void interpretControls() {
	if (controlMode < 0.25) mode = STAB;
	if (controlMode < 0.75) mode = STAB;
	if (controlMode > 0.75) mode = STAB;

	if (mode == AUTO) return; // pilot is not effective in AUTO mode

	if (controlThrottle < 0.05 && controlYaw > 0.95) armed = true; // arm gesture
	if (controlThrottle < 0.05 && controlYaw < -0.95) armed = false; // disarm gesture

	if (abs(controlYaw) < 0.1) controlYaw = 0; // yaw dead zone

	thrustTarget = controlThrottle;

	if (mode == STAB) {
		float yawTarget = attitudeTarget.getYaw();
		if (!armed || invalid(yawTarget) || controlYaw != 0) yawTarget = attitude.getYaw(); // reset yaw target
		attitudeTarget = Quaternion::fromEuler(Vector(controlRoll * tiltMax, controlPitch * tiltMax, yawTarget));
		ratesExtra = Vector(0, 0, -controlYaw * maxRate.z); // positive yaw stick means clockwise rotation in FLU
	}

	if (mode == ACRO) {
		attitudeTarget.invalidate(); // skip attitude control
		ratesTarget.x = controlRoll * maxRate.x;
		ratesTarget.y = controlPitch * maxRate.y;
		ratesTarget.z = -controlYaw * maxRate.z; // positive yaw stick means clockwise rotation in FLU
	}

	if (mode == RAW) { // direct torque control
		attitudeTarget.invalidate(); // skip attitude control
		ratesTarget.invalidate(); // skip rate control
		torqueTarget = Vector(controlRoll, controlPitch, -controlYaw) * 0.1;
	}

	if (mode == BEACON) { // use locator.ino to find beacon
		loopLocator();
    extern float getAngle();          // radians
    extern float getDistance();       // meters
    extern float getCurrentHeight();  // feet

    // Update global time for PID dt calculation
    extern float t;
    t = millis() / 1000.0f;

    float angleToBeacon = getAngle();
    float distanceToBeacon = getDistance();

    const float targetDistance = 0.5f; // meters
    const float maxPitch = 0.2f;       // radians

    // --- Forward/backward movement ---
    float pitchError = distanceToBeacon - targetDistance;
    float targetPitch = constrain(pitchError, -maxPitch, maxPitch);

    // --- Yaw control ---
    float yawError = angleToBeacon;
    float yawRateTarget = yawPID.update(yawError);

    // --- Attitude target ---
    float yawTarget = attitude.getYaw();
    attitudeTarget = Quaternion::fromEuler(Vector(0, -targetPitch, yawTarget));

    // --- Rate target ---
    ratesTarget.z = yawRateTarget;

    // =================================================
    // ALTITUDE HOLD (5 ft)
    // =================================================
    float currentHeight = getCurrentHeight(); // feet
    float heightError = TARGET_HEIGHT_FT - currentHeight;

    float thrustCorrection = ALT_KP * heightError;
    thrustTarget = ALT_HOVER_THRUST + thrustCorrection;

    thrustTarget = constrain(thrustTarget, ALT_MIN_THRUST, ALT_MAX_THRUST);

    // --- When close to beacon, hover instead of cutting thrust ---
    if (distanceToBeacon < targetDistance) {
        thrustTarget = ALT_HOVER_THRUST;
    }
	}	
}

void controlAttitude() {
	if (!armed || attitudeTarget.invalid() || thrustTarget < 0.1) return; // skip attitude control

	const Vector up(0, 0, 1);
	Vector upActual = Quaternion::rotateVector(up, attitude);
	Vector upTarget = Quaternion::rotateVector(up, attitudeTarget);

	Vector error = Vector::rotationVectorBetween(upTarget, upActual);

	ratesTarget.x = rollPID.update(error.x) + ratesExtra.x;
	ratesTarget.y = pitchPID.update(error.y) + ratesExtra.y;

	float yawError = wrapAngle(attitudeTarget.getYaw() - attitude.getYaw());
	ratesTarget.z = yawPID.update(yawError) + ratesExtra.z;
}


void controlRates() {
	if (!armed || ratesTarget.invalid() || thrustTarget < 0.1) return; // skip rates control

	Vector error = ratesTarget - rates;

	// Calculate desired torque, where 0 - no torque, 1 - maximum possible torque
	torqueTarget.x = rollRatePID.update(error.x);
	torqueTarget.y = pitchRatePID.update(error.y);
	torqueTarget.z = yawRatePID.update(error.z);
}

void controlTorque() {
	if (!torqueTarget.valid()) return; // skip torque control

	if (!armed) {
		memset(motors, 0, sizeof(motors)); // stop motors if disarmed
		setLED(4);
		return;
	}

	if (thrustTarget < 0.1) {
		motors[0] = 0.1; // idle thrust
		motors[1] = 0.1;
		motors[2] = 0.1;
		motors[3] = 0.1;
		return;
	}

	setLED(1);

	motors[MOTOR_FRONT_LEFT] = thrustTarget + torqueTarget.x - torqueTarget.y + torqueTarget.z;
	motors[MOTOR_FRONT_RIGHT] = thrustTarget - torqueTarget.x - torqueTarget.y - torqueTarget.z;
	motors[MOTOR_REAR_LEFT] = thrustTarget + torqueTarget.x + torqueTarget.y - torqueTarget.z;
	motors[MOTOR_REAR_RIGHT] = thrustTarget - torqueTarget.x + torqueTarget.y + torqueTarget.z;

	motors[0] = constrain(motors[0], 0, 1);
	motors[1] = constrain(motors[1], 0, 1);
	motors[2] = constrain(motors[2], 0, 1);
	motors[3] = constrain(motors[3], 0, 1);
}
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

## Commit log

2025-12-29 Enhance README with image gallery and BOM
    Added image gallery and Bill of Materials sections to README.
2025-12-29 Adjust component prices in README
    Updated prices for various components in the BOM.
2025-12-29 Fix battery price for drone in README
    Updated the price of the battery for the drone.
2025-12-29 Update BOM with new items and pricing
    Added JLCPCB Order to the BOM and updated prices.
    [Orbit BOM - Sheet1.csv]
2025-12-29 Update Bill Of Materials with new entries
    Added JLCPCB order for PCBs and updated total prices.
2025-12-29 Added STEP
    [Bottom.stl, Cap.step, Cap.stl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]
2025-12-29 Adjust JLCPCB order cost in README
    Updated JLCPCB order cost and total price in the BOM.
2025-12-29 Revise BOM with new items and price updates
    Updated the BOM with new items and adjusted prices.
    [Orbit BOM - Sheet1.csv]
2025-12-29 Add Hot Plate to BOM in README
    Added Hot Plate to the soldering materials list with pricing.
2025-12-29 Update BOM with new items and total prices
    Added new items to the BOM including a Hot Plate and updated total prices.
    [Orbit BOM - Sheet1.csv]
2025-12-30 Update LED quantities in README.md
2025-12-30 Revise BOM with updated items and prices
    Updated item list and quantities in the BOM.
    [Orbit BOM - Sheet1.csv]
2025-12-30 Revise Orbit BOM with new components and prices
    Updated item list with new entries and corrected quantities.
    [Orbit BOM - Sheet1.csv]
2025-12-30 Update Orbit BOM with new items and prices
    [Orbit BOM - Sheet1.csv]
2025-12-30 Add schematics and PCB details to README
    Added schematics and PCB details for Drone Control Board, Beacon Board, and UWB Module Board.
2026-01-04 Update BOM by removing Hot Plate and adjusting total
    Removed 'Hot Plate' entry and updated total cost.
2026-01-04 Revise BOM with updated items and pricing
    Updated item list and prices in the BOM.
    [Orbit BOM - Sheet1.csv]
2026-01-04 Revise quantities and prices in Orbit BOM
    Updated item quantities and prices in the BOM.
    [Orbit BOM - Sheet1.csv]
2026-01-05 Removed solder paste
2026-01-05 Update item list in Orbit BOM CSV
    [Orbit BOM - Sheet1.csv]
